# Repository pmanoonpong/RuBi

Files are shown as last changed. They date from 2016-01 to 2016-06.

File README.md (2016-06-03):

<h1>Design, simulation and development of RuBi, a bipedal platform for human-like locomotion studies</h1>

<h2>Description</h2>
RuBi is a study framework for human-like gaits part of the master thesis of Ignacio Torroba and Jorge Rodriguez. The idea is to create a robot that can perform actions like walking, running or jumping both in simulation in real life. One of the main advantages is the possibility of changing the springs in order to study SEA, PEA or SEA+PEA configurations with different springs.



In here, the description of the structure of the project is presented. The how-to for starting the simulation or bring up the robot can also be found in here. Some example controllers are given too.

It is supposed that you have a ROS Jade installed and working. This has only been tested in Ubuntu 15.04 and 14.04 under ROS Jade. To install it you can follow the official guides to be found in: http://wiki.ros.org/jade/Installation/Ubuntu. Remember that ROS Jade ONLY supports Trusty (14.04), Utopic (14.10) and Vivid (15.04) for Debian packages.

<h2>Project structure</h2>
The project has three basic folders:
  * <b>docs</b>: in here all the documents used for the deployment of the project are found. The master thesis is under the folder "report".
  * <b>media</b>: where all the media files as Photos, Videos, Presentations are stored.
  * <b>src</b>: the source folder where all the code, CAD models, robots description are.

The important folder for the user is the <b>src</b> folder and it follows the ROS structure convention. The code style is the imposed by the <i>Google Style</i> defined by the clang-code-model. The <b>build system</b> is catkin tools, and the environment is already included in the repo. This means that the user only need to clone the repo and everything will work "out-of-the-box" (notice the quotes there please).

In the source folder three kind of packages can be found:
  *   <b>ROS Jade needs</b>: Due to the use of ROS Jade, needed due to that in the description of the robots we use Jade-exclusive functions, some of the packages need to be compiled from the source. Those packages are copied as submodules in the repo and the correct branches are set with the installation script.
  *   <b>Robot descriptions</b>: Based on the Gazebo-ROS convention for describe the robots (http://gazebosim.org/tutorials/?tut=ros_overview). It is important to notice that TWO robots have been implemented: <b>RuBi</b> and <b>Dacbot</b>. Dacbot was created as a practice to finally create RuBi. Then the five folders are found for each robot.
    - robot_descrition: where all the files that describe the robot are found. If any CAD model is developed must be added in here.
    - robot_gazebo: used as a wrapper for bringing up the robot's simulation.
    - robot_bringup: used as a wrapper for bringing up the real robot.
    - robot_joint_controllers: originally called robot_controllers, though the name was change due to the lexical problem when defining "controller". This package offers the <i>joint controller</i> inside of ROS control. Ultimately what creates is a topic (e.g. /rubi/left_ankle_command) that can move the joint. This topic is then interfaced with the simulation or the real robot through a <i>hardware_interface</i>. Gazebo offers one, and the one from the real robot is called <b>locokit_hw</b> and can be found as another package within <i>src</i>.
    -   robot_controllers: Additionally, we add a new folder in which we deploy the controllers of the robot. Meaning, the controller that actually moves the robot for walking, running or jumping.
    
  *   <b>Miscellaneous</b>: these are <i>scripts</i> and <i>matlab_scripts</i>. The <b>scripts</b> folder includes the installation folder that, once the repo is cloned will download the submodules, install dependencies, etc... the <b>matlab_scripts</b> in where the actual Matlab programs used to size the motors, calculate the kinematic and dynamic models of the robot, etc.. are to be found.

<h2>First time</h2>
As explained before, inside of "src/scripts/" a script to be run the first time is found. This will download the submodules, install dependencies, etc... So:
``` bash
git clone URL_of_the_project
cd (path_to_project)/src/scripts
chmod +x install_first_time.sh
./install_first_time.sh
```
<h2>Robot definition</h2>
Inside the <i>rubi_definition</i> folder, several folders can be found. The suggested structured given in the ROS-Gazebo guides is followed. Two important things:
  * <b>CAD model</b>: the CAD model of the robot is to be found in the folder <b>meshes</b>. In here, the SolidWorks files are stored. At the same time, these follow the order of having the assembly file in the root folder and the parts in sub-folders. This will leave an assembly file called <i>Legs</i> that will load the Legs model and another one called <i>Legs with environment</i> where the robot is loaded along with the treadmill.
  * <b>Xacro</b>: the robot is defined in the URDF format. This is needed because ROS Control uses it. The robot is coded using Xacro because it simplifies the wrtting and allows conditional expression. Check the flags out inside of the <i>rubi.xacro</i> file. These add some functionality like scaling the robot or create the rotational holder, among others.

<h2>Develop controllers</h2>
In order to facilitate the development of new controllers two example controllers are given inside of RuBi. First clarify that ALL the controllers of a robot MUST be in one folder. This was decided due to the experience obtained during the use of LPZ Robots. 

To deploy a new controller just add the source into the <b>src</b> folder and add it into the CMakeList.txt. Is a ROS package, so more information can be found in Google. One of the example controllers show how to use GoRobots in it.

Remember that for using GoRobots an environmental variable called <i>GOROBOTS</i> must exist. This can be done by adding to the <i>.bashrc</i> file found in the home folder:
``` bash
export GOROBOTS=/path/to/gorobots
```

All the packages in the catkin environment are compiled introducing the next comand in any of the sub-directories of the project:
``` bash
catkin build
```

<h2>Bring up the simulation</h2>
The simulation can be loaded by opening a terminal and writing:
``` bash
roslaunch rubi_gazebo rubi.world
```
This will load the Gazebo environment, the model, the joint controllers and the plugins associated. Once finished, the controllers can be started.

<h2>Bring up the real robot</h2>
The real robot can be loaded by opening a terminal and writing:
``` bash
roslaunch rubi_bringup rubi_bringup.launch
```
This will load the Locokit interface, the model, the joint controllers and the plugins associated. Once finished, the controllers can be started.

<h2>Contributors</h2>
<b>Supervisors: </b>
  * Poramate Manoonpong: poma@mmmi.sdu.dk
  * Jørgen Christian Larsen: jcla@mmmi.sdu.dk

<b>Students: </b>
  * Jorge Rodriguez Marin: jorge.rguez.marin@gmail.com
  * Ignacio Torroba Balmori: ignaciotorroba@hotmail.com

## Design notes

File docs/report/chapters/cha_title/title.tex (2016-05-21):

%!TEX root = ../../report.tex

% Title Page
\begin{titlepage}

	\begin{center}
	\\

	\vspace{0.3cm}
	\textbf{\institute}\\

	\textmd{\department}\\
	\textmd{\program}  %- \textmd{\course}
	% \makebox[0pt][l]{
	% 	\hspace{-14cm}
	%   \raisebox{-\totalheight}[0pt][0pt]{
	%   	\includegraphics[height=180mm]{figures/legs_technical_drawing.pdf}
	%   }
	\makebox[0pt][l]{
		\hspace{-20.5cm}
	  \raisebox{-\totalheight}[0pt][0pt]{
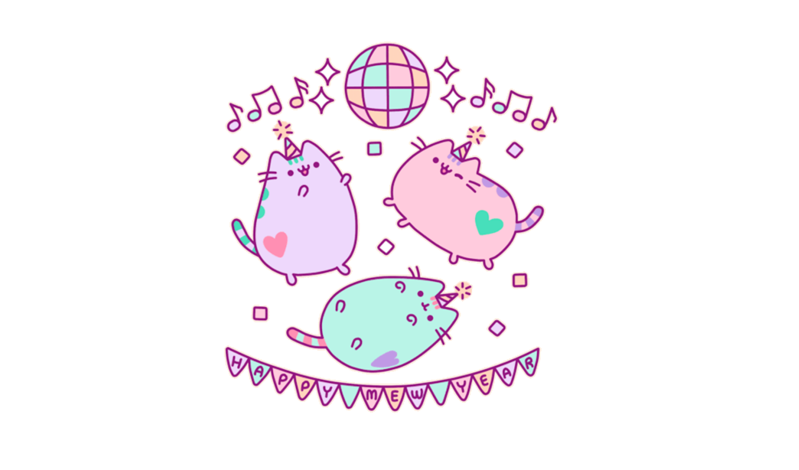
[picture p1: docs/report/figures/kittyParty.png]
	  	
	  }
	}\\[4cm]

	\vspace{0.4cm}
	{\huge \bfseries \documentTitle}
	\\
	\vspace{0.5cm}
	{\large \documentType}
	\\[2cm]

	\begin{tabular}{c}
	 \makebox[4cm]{\emph{Authors}} \\
	 \makebox[4cm]{\authorOne} \\
	 \makebox[4cm]{\authorTwo} \\
	\end{tabular}

	\vfill
	{\large \today}
	\end{center}

\end{titlepage}

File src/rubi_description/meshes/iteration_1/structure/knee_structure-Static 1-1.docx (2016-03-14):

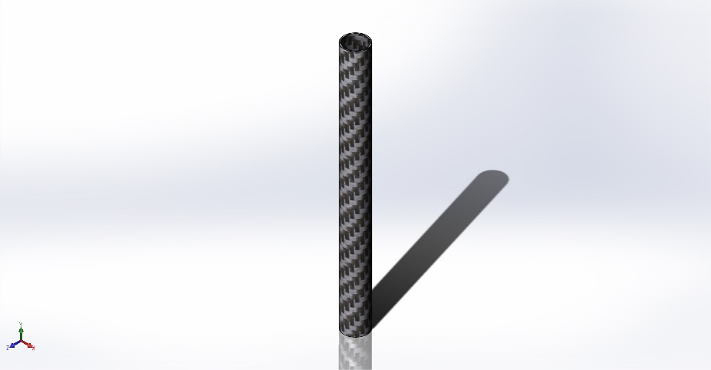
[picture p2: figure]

Simulation of knee_structure

Date: Monday, March 14, 2016
Designer: Jorge Rodriguez

Study name: Static 1

Analysis type: Static
Description No Data

# Assumptions

# Model Information

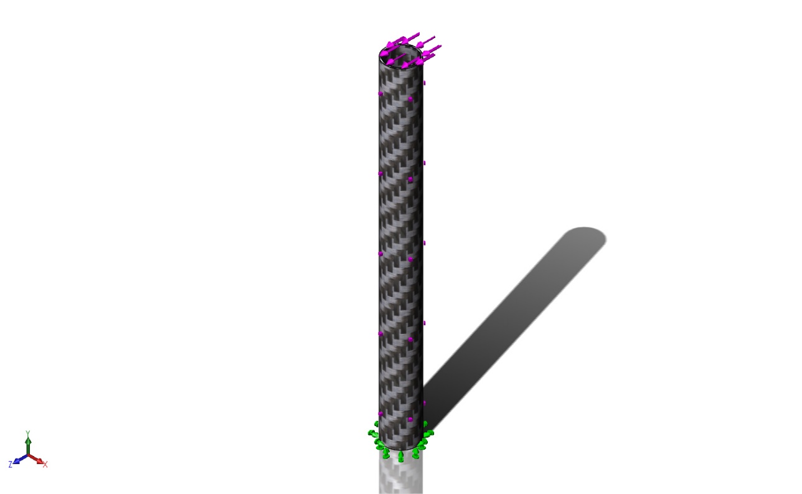
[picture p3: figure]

Model name: knee_structure

Current Configuration: Default

Solid Bodies
Document Name and Reference | Treated As | Volumetric Properties | Document Path/Date Modified

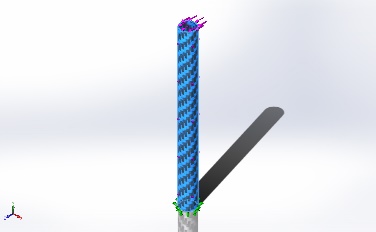
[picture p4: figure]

Boss-Extrude1 | Solid Body | Mass:0.0203042 kg Volume:1.26901e-005 m^3 Density:1600 kg/m^3 Weight:0.198982 N | D:\Drive\Projects\Legs\src\legs_description\meshes\Iteration 1\structure\knee_structure.SLDPRT Mar 13 20:21:27 2016

# Study Properties

Study name | Static 1
Analysis type | Static
Mesh type | Solid Mesh
Thermal Effect: | On
Thermal option | Include temperature loads
Zero strain temperature | 298 Kelvin
Include fluid pressure effects from SolidWorks Flow Simulation | Off
Solver type | FFEPlus
Inplane Effect: | Off
Soft Spring: | Off
Inertial Relief: | Off
Incompatible bonding options | Automatic
Large displacement | Off
Compute free body forces | Off
Friction | Off
Use Adaptive Method: | Off
Result folder | SolidWorks document (D:\Drive\Projects\Legs\src\legs_description\meshes\Iteration 1\structure)

# Units

Unit system: | SI (MKS)
Length/Displacement | mm
Temperature | Kelvin
Angular velocity | Rad/sec
Pressure/Stress | N/m^2

# Material Properties

Model Reference | Properties | Components

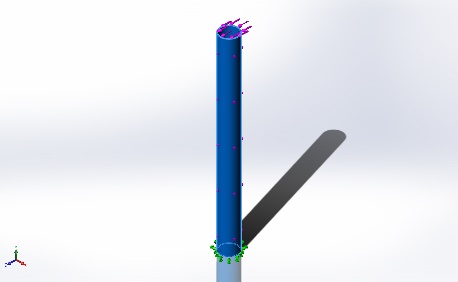
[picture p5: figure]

| Name: Toray T700 Model type: Linear Elastic Isotropic Default failure criterion: Unknown Tensile strength: 4e+008 N/m^2 Compressive strength: 3.5e+008 N/m^2 Elastic modulus: 1.9e+010 N/m^2 Poisson's ratio: 0.14 Mass density: 1600 kg/m^3 Shear modulus: 4.6e+009 N/m^2 | SolidBody 1(Boss-Extrude1)(knee_structure)

Curve Data:N/A

# Loads and Fixtures

Fixture name | Fixture Image | Fixture Details

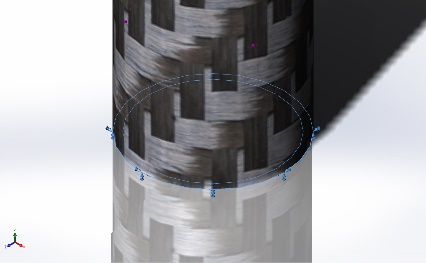
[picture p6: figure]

Fixed-1 | | Entities: 1 face(s) Type: Fixed Geometry

Resultant Forces

Components | X | Y | Z | Resultant
Reaction force(N) | 0.0268427 | 0.0375519 | -293.247 | 293.247
Reaction Moment(N.m) | 0 | 0 | 0 | 0

Load name | Load Image | Load Details

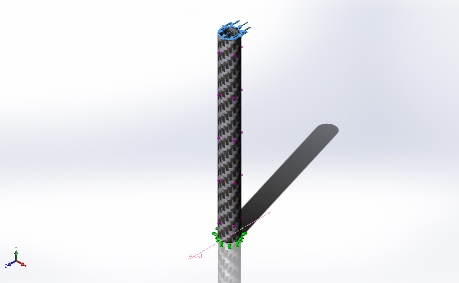
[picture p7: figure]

Force-1 | | Entities: 1 face(s) Reference: Axis1 Type: Apply force Values: ---, ---, -293.3 N

# Connector Definitions

No Data

# Contact Information

No Data

# Mesh Information

Mesh type | Solid Mesh
Mesher Used: | Curvature based mesh
Jacobian points | 4 Points
Maximum element size | 1.59686 mm
Minimum element size | 1.59686 mm
Mesh Quality | High

## Mesh Information - Details

Total Nodes | 63496
Total Elements | 31816
Maximum Aspect Ratio | 7.2328
% of elements with Aspect Ratio < 3 | 99.1
% of elements with Aspect Ratio > 10 | 0
% of distorted elements(Jacobian) | 0
Time to complete mesh(hh;mm;ss): | 00:00:04
Computer name: | JORGE-WINDOWS

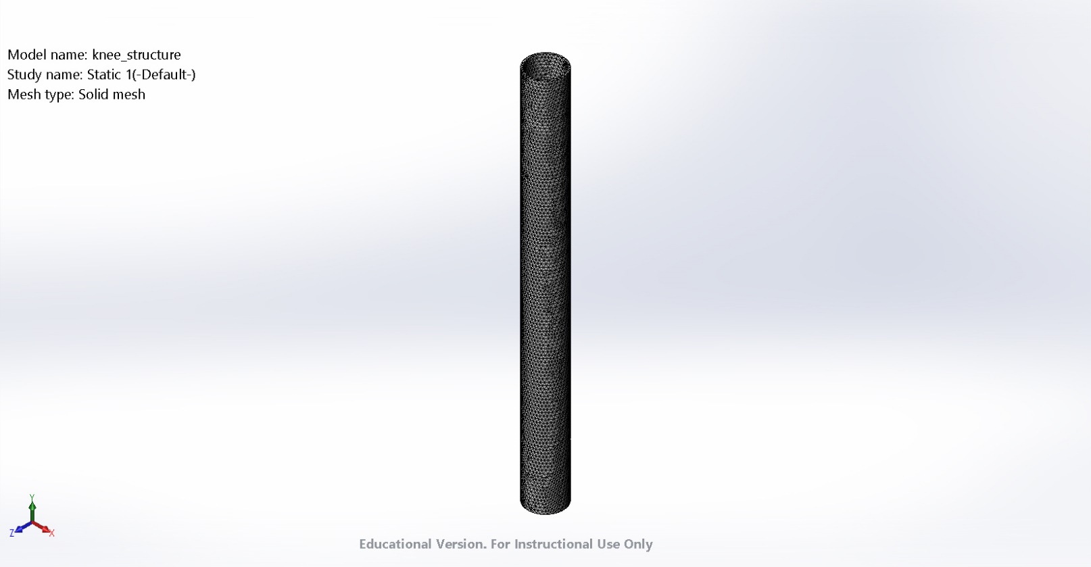
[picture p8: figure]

## Mesh Control Information:

Mesh Control Name | Mesh Control Image | Mesh Control Details

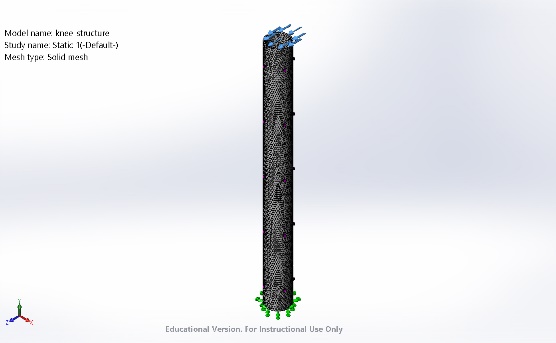
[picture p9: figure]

Control-1 | | Entities: 1 component(s) Units: mm Size: 1.59686 Ratio: 1.5

# Sensor Details

No Data

# Resultant Forces

## Reaction Forces

Selection set | Units | Sum X | Sum Y | Sum Z | Resultant
Entire Model | N | 0.0268427 | 0.0375519 | -293.247 | 293.247

## Reaction Moments

Selection set | Units | Sum X | Sum Y | Sum Z | Resultant
Entire Model | N.m | 0 | 0 | 0 | 0

# Beams

No Data

# Study Results

Name | Type | Min | Max
Stress1 | VON: von Mises Stress | 1.7183e+006 N/m^2 Node: 38677 | 2.45927e+008 N/m^2 Node: 4900

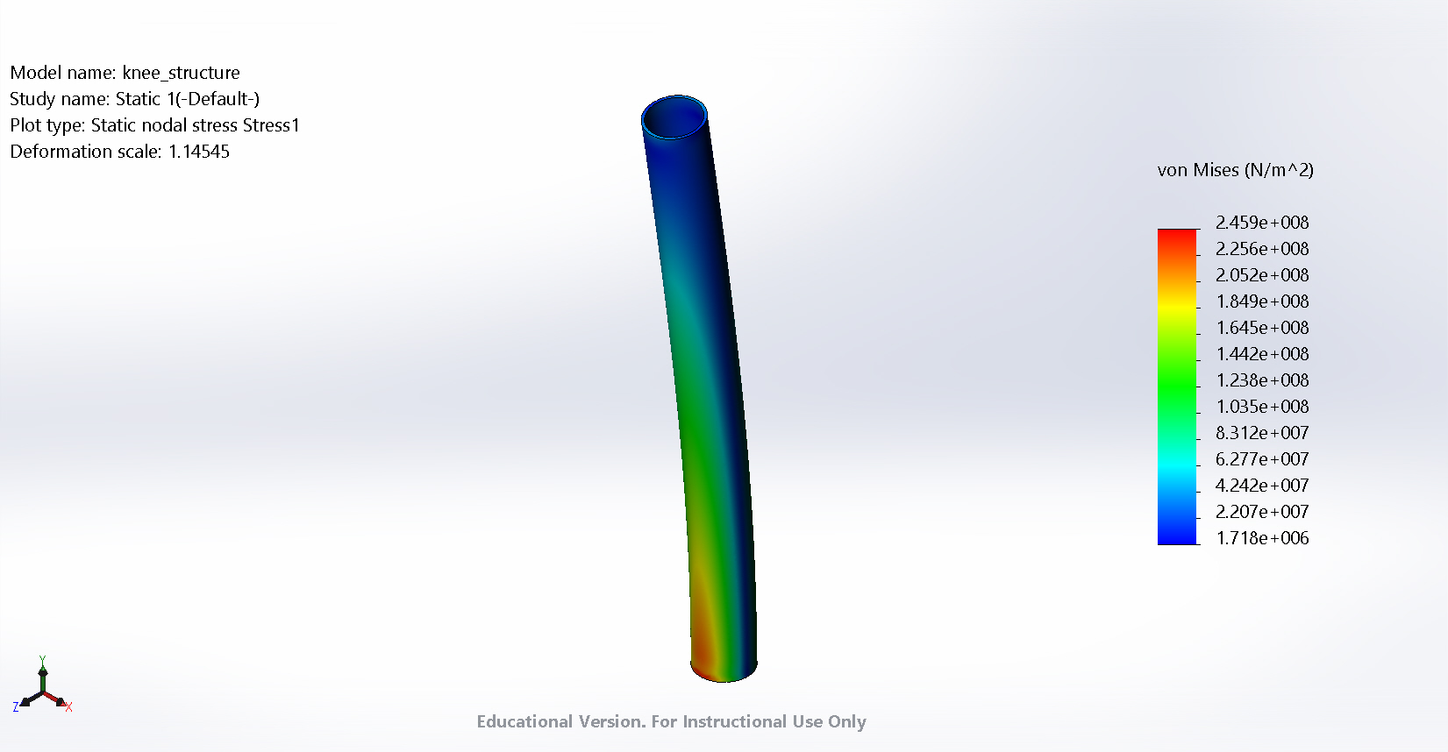
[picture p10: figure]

knee_structure-Static 1-Stress-Stress1

Name | Type | Min | Max
Displacement1 | URES: Resultant Displacement | 0 mm Node: 42 | 18.6053 mm Node: 19

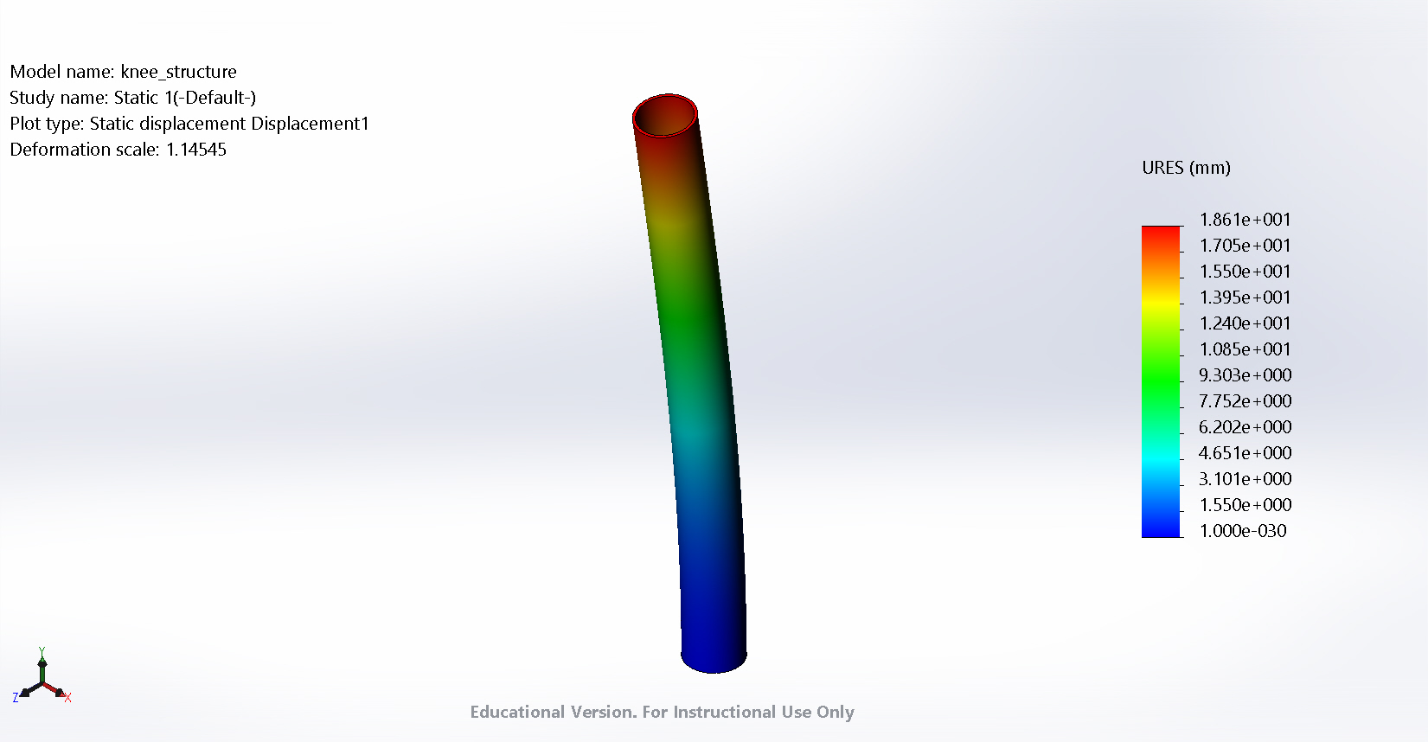
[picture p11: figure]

knee_structure-Static 1-Displacement-Displacement1

Name | Type | Min | Max
Strain1 | ESTRN: Equivalent Strain | 7.96386e-005 Element: 28451 | 0.00900996 Element: 23735

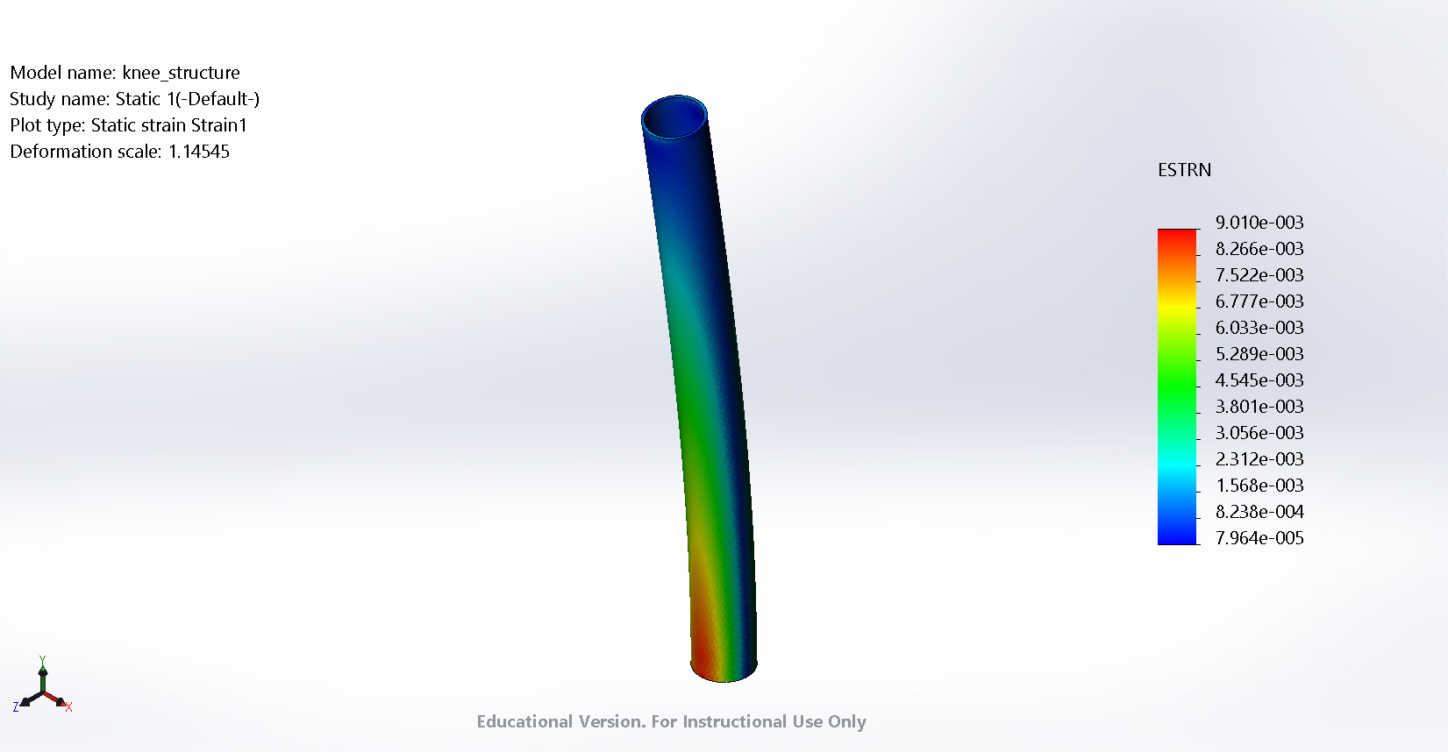
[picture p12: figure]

knee_structure-Static 1-Strain-Strain1

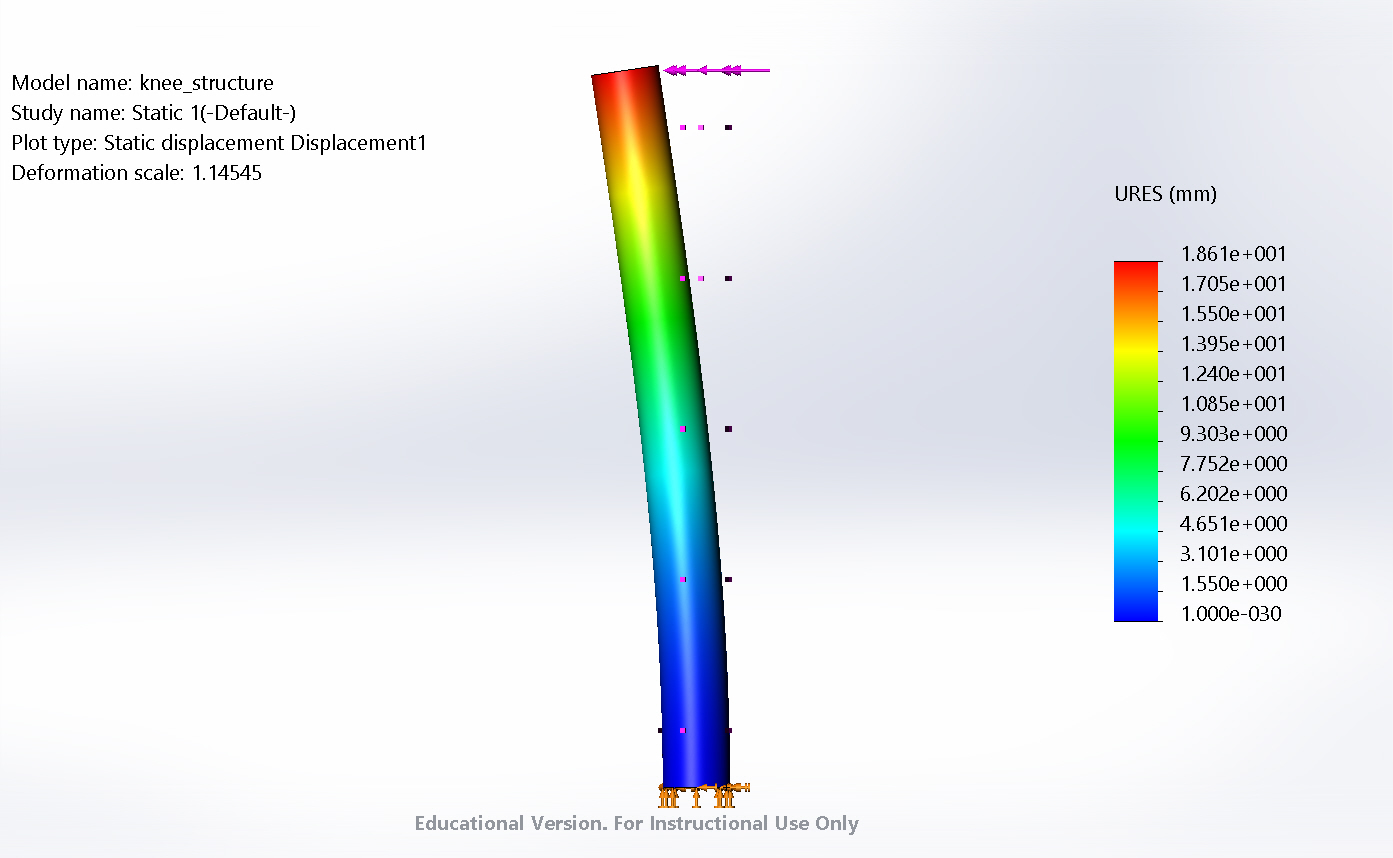
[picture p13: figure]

Image-1

# Conclusion

Analyzed with SolidWorks Simulation Simulation of knee_structure 13

Analyzed with SolidWorks Simulation Simulation of knee_structure 1

Jorge Rodriguez 14-Mar-16

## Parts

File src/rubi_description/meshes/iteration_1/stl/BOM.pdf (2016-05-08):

Part | Quantity
4 | motor_pulley_T2,5_19teeth
1 | hip
2 | hip_pinion
1 | left_hip_lower
1 | left_ankle_spring_series_with_pulley
1 | left_ankle_upper
1 | left_foot
1 | left_knee_lower
1 | left_knee_spring_series_with_pulley
1 | left_knee_upper
1 | right_hip_lower
1 | right_ankle_spring_series_with_pulley
1 | right_ankle_upper
1 | right_foot
1 | right_knee_lower
1 | right_knee_spring_series_with_pulley
1 | right_knee_upper

# BOM

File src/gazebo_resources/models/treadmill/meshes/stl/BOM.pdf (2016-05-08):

Part | Quantity
1 | Interface Robot holder
1 | Printed Parts Profile Robot
1 | Printed Parts Profile Treadmill

# BOM

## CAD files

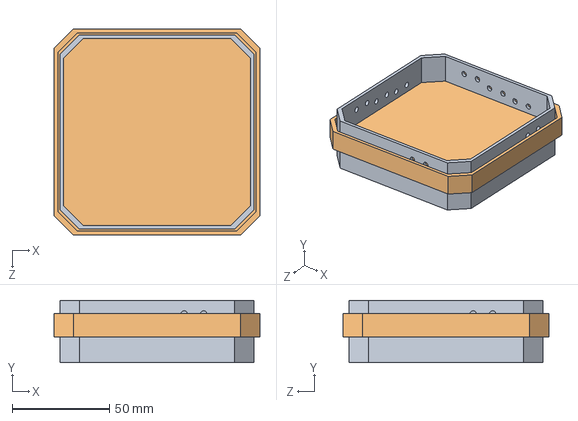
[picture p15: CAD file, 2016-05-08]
src/gazebo_resources/models/jumping_platform/meshes/Assem1.SLDASM
106.0 x 32.0 x 106.0 mm
bottom
top

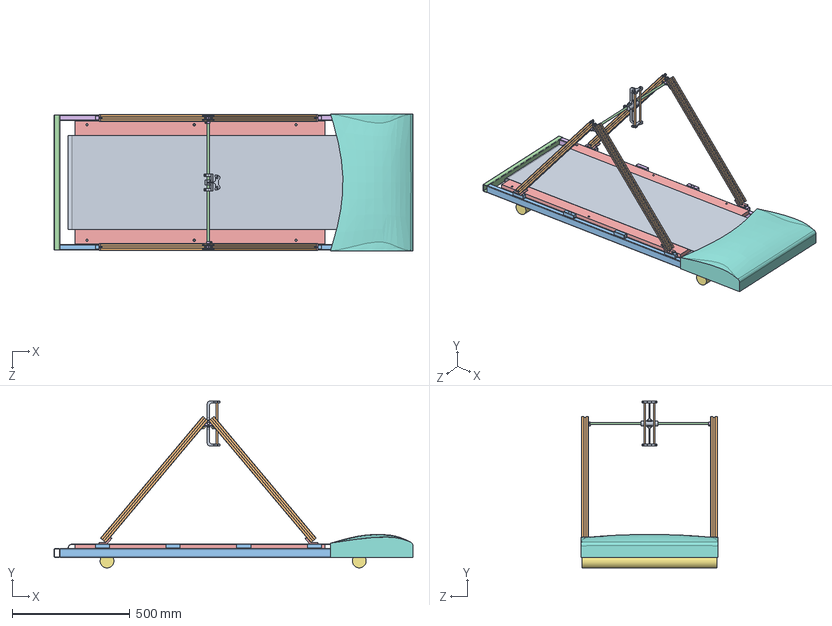
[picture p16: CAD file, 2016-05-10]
src/gazebo_resources/models/treadmill/meshes/treadmill.SLDASM
1523.0 x 707.3 x 580.0 mm
running_area
Bosch Profile - 30x30 x 4
Structure - right side
Structure - front x 2
Structure - table
MirrorStructure - right side
Structure - legs x 2
Cover
Interface - Robot holder
Interface - Jumping rods x 2
bearing_S 6000-2RS_618-9991 x 2
Interface - Structure rod
Printed Parts - Profile - Treadmill x 4
Printed Parts - Profile - Robot x 2
DIN 912 M6 x 10 --- 10N x 8
klee M3x5 x 2
DIN 912 M3 x 6 --- 6N x 2

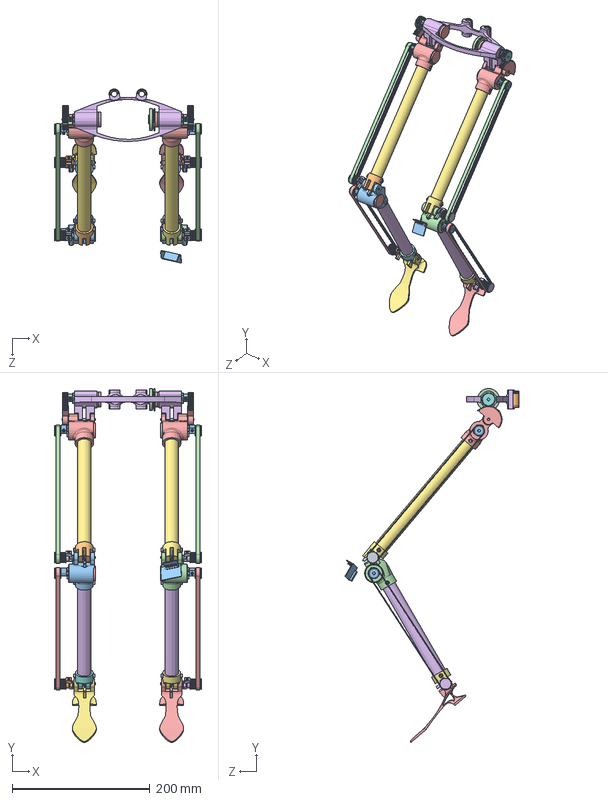
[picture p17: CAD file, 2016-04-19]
src/legs_description/meshes/iteration_1/Legs.SLDASM
213.8 x 514.5 x 253.3 mm
DIN 912 M2.5 x 8 --- 8N x 18
klee M3x5 x 18
ISO 4029 - M3 x 6-S x 18
Steel External Circlip 3mm x 8
hip_motor_holder_left x 2
hip
hip_rod x 2
hip_pinion
bearing_SS623-2RS_893-7420 x 24
Bearing - LBBR8 341-1504 x 2
T2,5 6mm 19teeth x 4
belt_gt2_hip x 2
belt_gt2_knee x 2
DIN 912 M3 x 6 --- 6N x 12
left_knee_upper
left_knee_rod x 2
left_knee_spring_series_holder
spring_knee_serial
spring_knee_parallel
knee_motor_holder_left
foot_left
foot_spring_series_holder_left
ankle_left
ankle_rod x 2
spring_ankle_parallel
spring_ankle_serial
Maxon - Gearbox 143976 x 6
Maxon - Interface x 6
knee_structure x 2
hip_structure x 2
Mirrorspring_knee_serial
Mirrorleft_knee_spring_series_holder
Mirrorleft_knee_upper
Mirrorknee_motor_holder_left
Mirrorhip_pinion
Mirrorspring_ankle_serial
Mirrorspring_ankle_parallel
Mirrorfoot_left
Mirrorankle_left
Mirrorspring_knee_parallel
Mirrorfoot_spring_series_holder_left
Maxon - Extensor

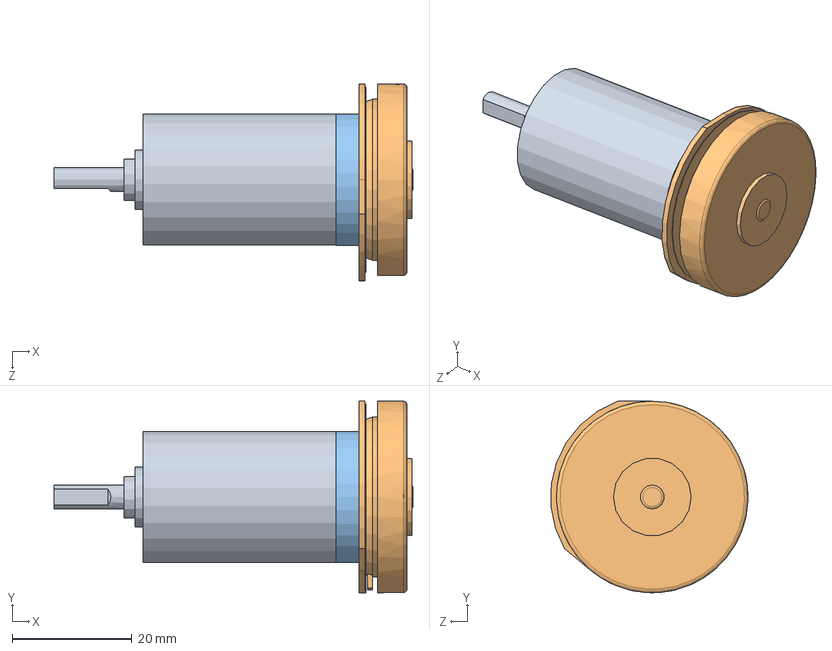
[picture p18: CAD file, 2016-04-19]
src/rubi_description/meshes/iteration_1/motors/Maxon - Combination 432941.SLDASM
60.0 x 32.0 x 32.9 mm
Maxon - Gearbox 143976
Maxon - Motor 339260
Maxon - Interface

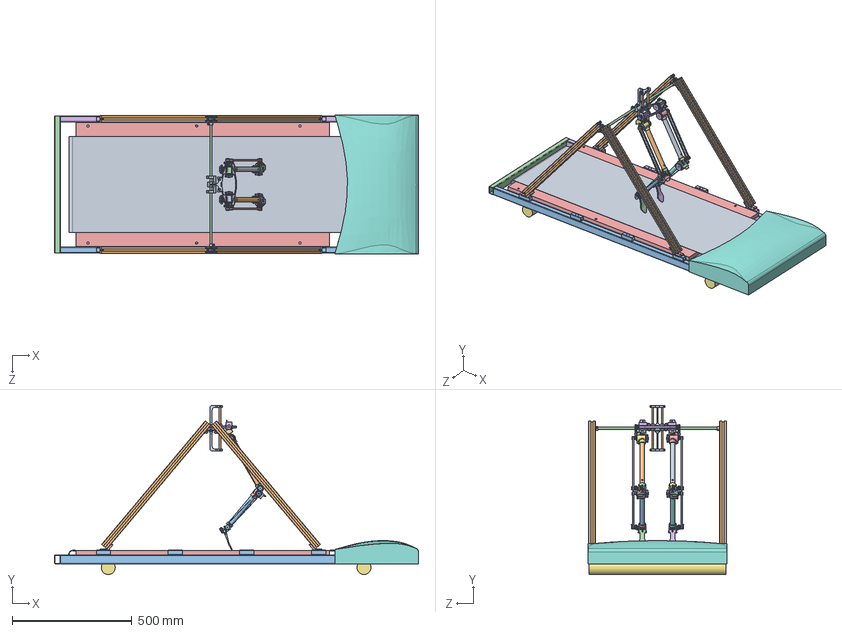
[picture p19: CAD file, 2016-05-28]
src/rubi_description/meshes/iteration_1/Rubi and Environment.SLDASM
1523.0 x 707.3 x 580.0 mm
running_area
Bosch Profile - 30x30 x 4
Structure - right side
Structure - front x 2
Structure - table
MirrorStructure - right side
Structure - legs x 2
Cover
Interface - Robot holder
Interface - Jumping rods x 2
bearing_S 6000-2RS_618-9991 x 2
Interface - Structure rod
Printed Parts - Profile - Treadmill x 4
Printed Parts - Profile - Robot x 2
DIN 912 M6 x 10 --- 10N x 8
klee M3x5 x 20
DIN 912 M3 x 6 --- 6N x 14
DIN 912 M2.5 x 8 --- 8N x 18
ISO 4029 - M3 x 6-S x 18
Steel External Circlip 3mm x 8
left_hip_lower
hip
hip_rod x 2
hip_pinion
bearing_SS623-2RS_893-7420 x 24
Bearing - LBBR8 341-1504 x 2
motor_pulley_T2,5_19teeth x 3
Maxon - Extensor x 3
belt_gt2_hip x 2
belt_gt2_knee x 2
left_knee_upper
knee_rod x 2
left_knee_spring_series_with_pulley
spring_knee_serial
spring_knee_parallel
left_knee_lower
DIN 912 M2.5 x 16 --- 16N x 4
left_foot
left_ankle_spring_series_with_pulley
left_ankle_upper
ankle_rod x 2
spring_ankle_parallel
spring_ankle_serial
Contact sensor x 2
Maxon - Gearbox 143976 x 6
Maxon - Motor 339260 x 6
Maxon - Interface x 6
knee_structure
hip_structure
Mirrorspring_knee_serial
right_knee_spring_series_with_pulley
right_knee_upper
right_knee_lower
Mirrorhip_pinion
right_hip_lower
Mirrorspring_ankle_serial
Mirrorspring_ankle_parallel
Mirrorhip_structure
Mirrorknee_structure
right_foot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

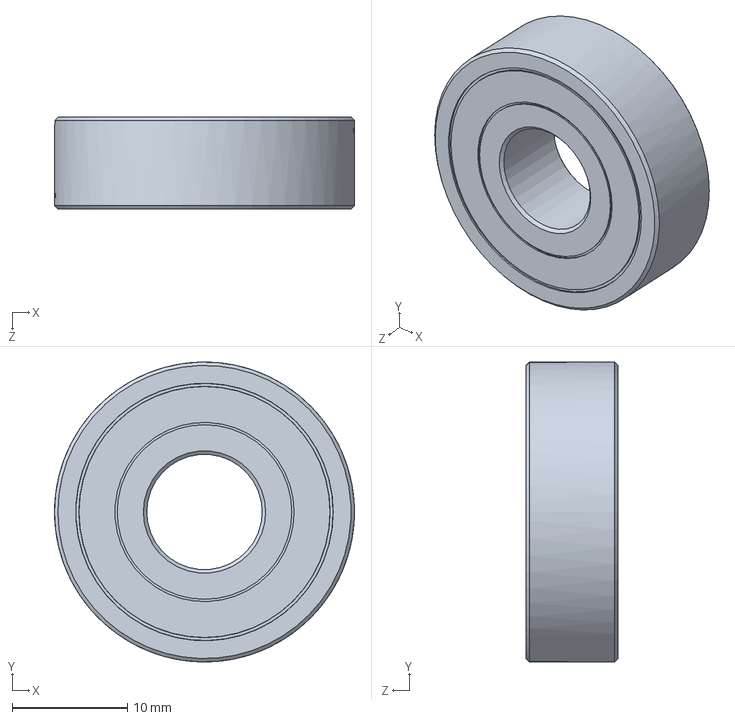
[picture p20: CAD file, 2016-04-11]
src/gazebo_resources/models/treadmill/meshes/Bearings/bearing_S 6000-2RS_618-9991.SLDPRT
26.0 x 26.0 x 8.00 mm

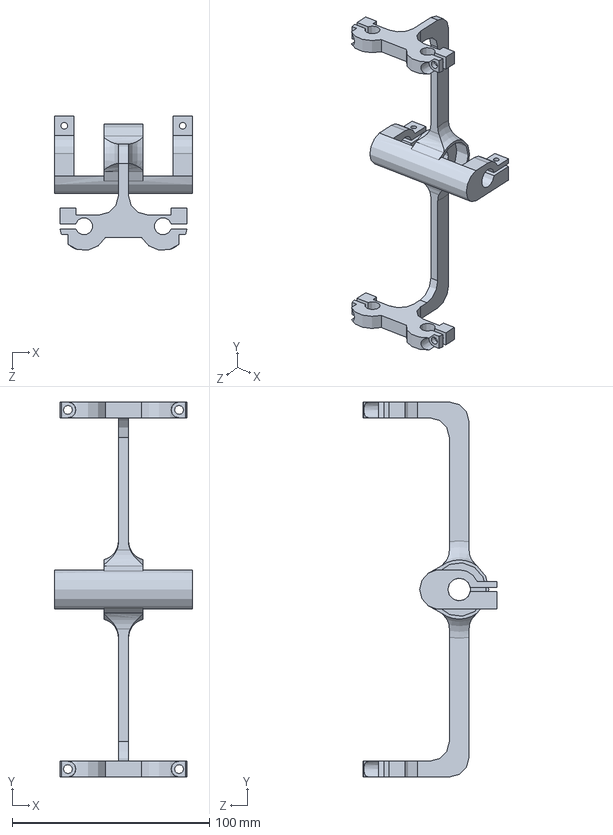
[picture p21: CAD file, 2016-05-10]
src/gazebo_resources/models/treadmill/meshes/Interface/Interface - Robot holder.SLDPRT
70.0 x 190.0 x 68.0 mm

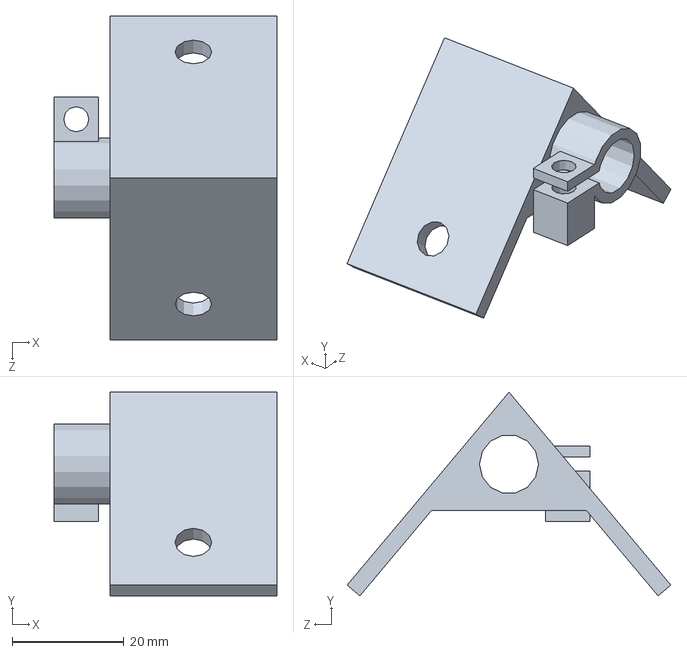
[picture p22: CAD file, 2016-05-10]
src/gazebo_resources/models/treadmill/meshes/Printed Parts/Printed Parts - Profile - Robot.SLDPRT
40.0 x 36.5 x 58.1 mm

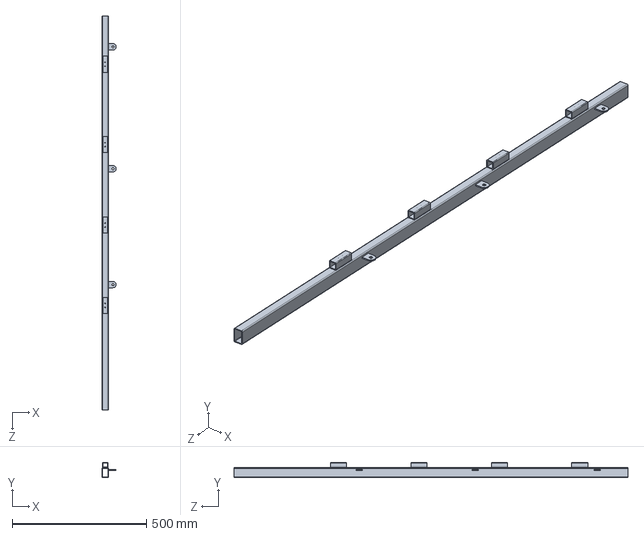
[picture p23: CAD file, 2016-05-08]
src/gazebo_resources/models/treadmill/meshes/Structure/Structure - right side.SLDPRT
54.0 x 57.0 x 1470.0 mm

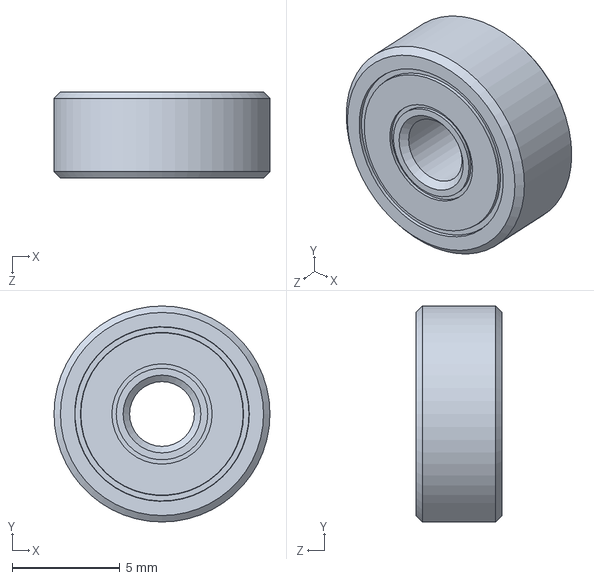
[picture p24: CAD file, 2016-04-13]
src/rubi_description/meshes/iteration_1/bearings/bearing_SS623-2RS_893-7420.SLDPRT
10.0 x 10.0 x 4.00 mm

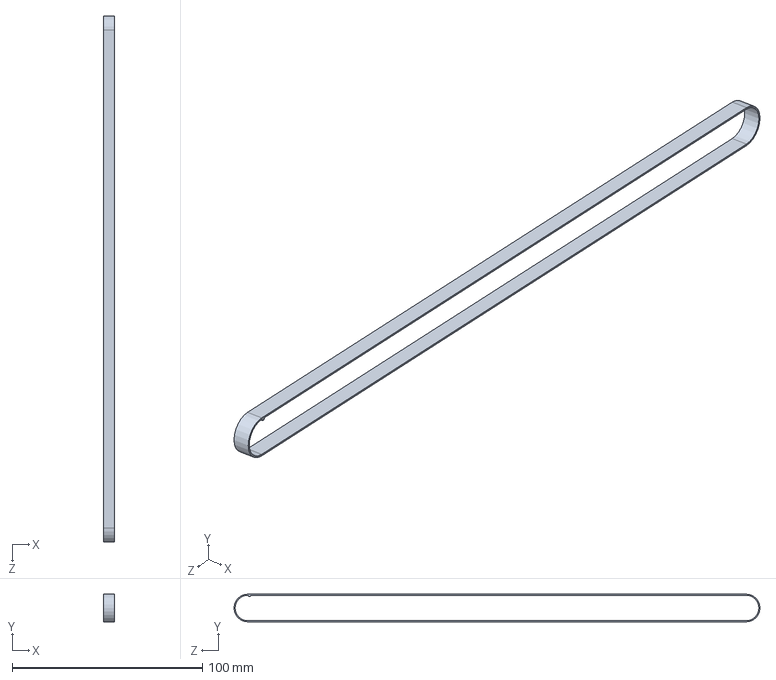
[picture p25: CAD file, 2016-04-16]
src/rubi_description/meshes/iteration_1/belt/belt_t2,5_14.6.SLDPRT
6.00 x 14.6 x 276.6 mm

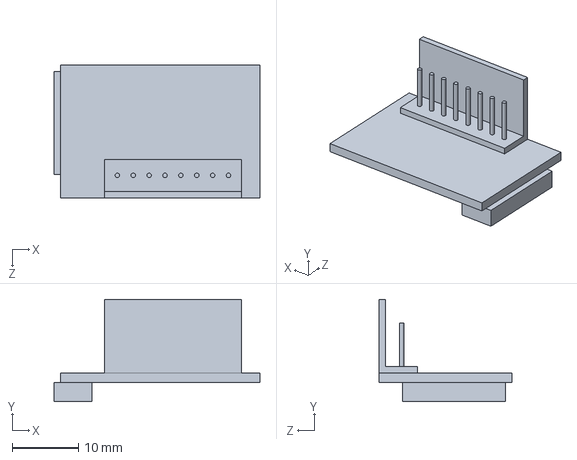
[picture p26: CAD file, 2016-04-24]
src/rubi_description/meshes/iteration_1/electronics/MirrorMaxon - Extensor.SLDPRT
31.0 x 15.4 x 20.0 mm

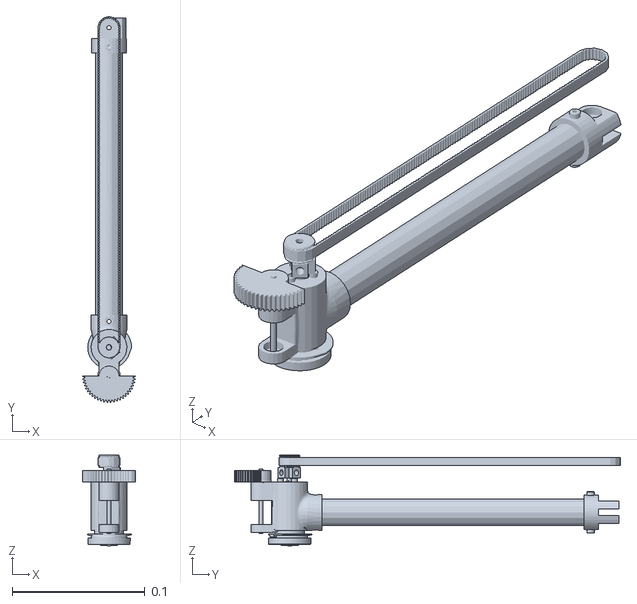
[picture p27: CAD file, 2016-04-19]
src/rubi_description/meshes/iteration_1/gazebo/left_upper_limb_visual.stl
0.04 x 0.29 x 0.0681

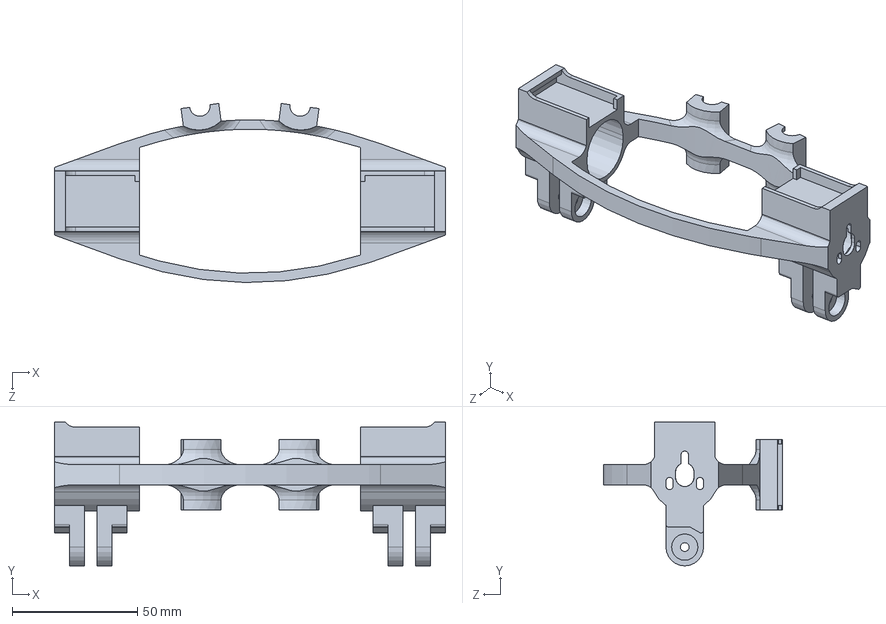
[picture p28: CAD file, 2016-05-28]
src/rubi_description/meshes/iteration_1/hip/hip.SLDPRT
156.0 x 57.4 x 71.4 mm

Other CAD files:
src/gazebo_resources/models/treadmill/meshes/stl/Printed Parts - Profile - Robot.STL
src/rubi_description/meshes/iteration_1/left_leg/ankle/left_ankle_spring_series_with_pulley.SLDPRT
src/rubi_description/meshes/iteration_1/left_leg/hip/hip_pinion.SLDPRT
src/rubi_description/meshes/iteration_1/left_leg/knee/left_knee_spring_series_with_pulley.SLDPRT
src/gazebo_resources/models/jumping_platform/meshes/bottom.SLDPRT
src/gazebo_resources/models/jumping_platform/meshes/top.SLDPRT
src/gazebo_resources/models/treadmill/meshes/Bosch Profile - 30x30.SLDPRT
src/gazebo_resources/models/treadmill/meshes/Fasteners/DIN 912 M3 x 6 --- 6N.sldprt
src/gazebo_resources/models/treadmill/meshes/Fasteners/DIN 912 M6 x 10 --- 10N.sldprt
src/gazebo_resources/models/treadmill/meshes/Interface/Interface - Jumping rods.SLDPRT
src/gazebo_resources/models/treadmill/meshes/Interface/Interface - Structure rod.SLDPRT
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

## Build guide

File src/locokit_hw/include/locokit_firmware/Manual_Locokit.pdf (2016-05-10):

## Manual Locokit over-a-network controller:

The project is made to control Locokit robot by using an interface that connects with the robot over a wireless connection. The project consists of two programs: the server program and the client program. The server program is executed on the robot's processor. The client program provides an interface that enables the user to send commands to the server to be executed. The used protocol for the connection is TCP to make sure that all transmitted information are preserved.

Running the system and establishing the connection:

The following steps demonstrate how the system should be used:

1) connecting to a wireless network:
The robot connects automatically with the wireless network “gumstix-network” and it has the IP 192.168.2.4 (the IP could be different for a different locokit robot instance). Connect the client computer to the same network and give your pc different IP address.
(for more details: http://modular.tek.sdu.dk/index.php?page=connecting-to-locokit-using-wifi)
2) Establish an SSH session:
open a terminal and write:
ssh root@192.168.2.4 (the IP could be different for a different locokit robot instance)
to open an ssh session. No password is needed for the login so just press enter when you are asked about it.
3) Run the server project:
open the following directory:
$: users/Bassel/wlan_controller
inside this folder there are the following files:
Makefile //the configuration of the compiling process actuateMotors.c //the server code
loco-settings.cfg //the robot configuration file
the code can be compiled by entering the folder and enter: make all
the compiler generate a file called “actuateMotors“
(if you are using a new instance of the robot, add those files to any directory and compile them and continue. The files can be found under utils/real_robots/locokit)
- run the server program by typing “./actuateMotors”. The server at that point will just wait for a connection from the client (socket). you should see the sentence “waiting for connections” on the terminal after running the executable file.
4) Run the Client program:

To connect the client program just open ANOTHER terminal and go to your client program executable file and run it.
NOTE: the server program should be already executed before the client program starts.
5) sending commands:
use your “LocoKitInterface” class to send and receive commands between the client and the server. The available commands will be showed in the next section.
6) Closing:
make sure that the constructor of your client LocoKitInterface object is called before you terminate your client program (i.e. use delete if you define a pointer to the object LocoKitInterface). After the client program is terminated the server program can be terminated also.

How to use the interface:

Two classes (LocoKitInterface and ConnectionClass) are provided to the user. These two classes enable the client to send commands to the server. The user should instantiate the class “LocoKitInterface” which uses the class ConnectionClass as a lower layer to send commands.

Steps:
1) define an LocoKitInterface object:

LocoKitInterface LKI; //define an object
if (LKI.establish_connection() == -1) {
printf("Error from LocoKitInterface: a connection couldn't be established...\n");
return -1;
}
2) use the available functions:
e.g. setActuatorPWM

LKI.setActuatorPWM(pmw, 2);

Available functions (Client side):

int establish_connection();
//Establish the connection with the server side. //Return 0 if successful, -1 for errors.

int setActuatorPWM(float pwm, int actuator); //Set the PWM of an actuator. //Parameters:
//pwm: The PWN in the range from -1024 to 1024 //Actuator: The ID of the actuator
//Return 0 if successful, -1 for errors.

int setActuatorStopped(int actuator); //Stop an actuator.
//Parameters:
//actuator: The ID of the actuator
//Returns: 0 if successful, -1 for errors

int setConstantSpeedInterpolatingFunction (int actuator, float period, float phaseOffset, int directionNegative);
//Set the motor control interpolation values.
//Parameters:
//actuator: The motor to control
//period: The period time in seconds
//phaseOffset: The phaseOffset in degrees
//directionNegative: The direction of rotation, 0 for rotation in positive direction 1 for negative
//Returns: 0 if successful, -1 for errors

int getNumberOfSensors();
//returns the number of sensors.
//Returns 0 if successful, -1 for errors

int getSensorValueRawFloat(int sensor, float &sensor_value);
//get the current unmodified value of the sensor (returned in the "sensor_value" parameter)
//Parameters: The ID of the sensor
//returns: 0 if successful, -1 for errors
//sensors ID numbers:
//sensor (0) ---> acc on x
//sensor (1) ---> acc on y
//sensor (2) ---> acc on z //sensor (3) ---> gyo x
//sensor (0) ---> gyo y
//sensor (0) ---> gyo z int updateSensorValueRawFloat_array();
//provides 6 values that are pointed out in the previous
//function (getSensorValueRawFloat ID:0..5) in one array and at the same order. //these values are saved in the public member sensory_inputs.
//returns 0 if successful, -1 otherwise
int | getActuatorVelocity(int | actuator, float& | velocity);
//Get the velocity of an actuator.
//Parameters:
//actuator: the ID of the actuator
//velocity: the | velocity in degrees per second in | the parameter “velocity”
//returns 0 if successful, -1 otherwise

int getActuatorPosition(int actuator, float& position);
//Get the current position of an actuator.
//Parameters:
//actuator: The ID of the actuator
//provide the position in degrees in the parameter “position” //returns 0 if successful, -1 otherwise

int getActuatorPWM(int actuator, float& PWM_value); //get the PWM of an actuator
//Parameters:
//actuator: the ID of the actuator
//provides the PWM in the parameter "PMW_value" //returns 0 if successful, -1 otherwise

int getSensorValue(int sensor, float &sensor_value); //Get current sensor value.
//Parameters:
//sensor: the ID of the sensor
//provides the current value of the sensor in the parameter "sensor_value" //returns 0 if successful, -1 otherwise

int resetSensorValue(int sensor);
////Reset a sensor. The current sensor value is used as offset for future calls to getSensorValue but not getSensorValueRaw.
//Parameters:
//sensor: the ID of the sensor
//returns 0 if successful, -1 otherwise

int terminate_connection_with_server();

//This function is called to terminate the connection with the server. It send a command to the //server to terminate the server program also

### Available Functions (Server side):

void PWM_control_routine(int act_number, float pwm);
//applying the pwm value on the targeted actuator.
It takes the actuator ID as an input in addition to the pwm value

void ConstantSpeedInterpolatingFunction_control_routine(int act_number, float period, float phaseoffset, int direction);
//applying the ConstantSpeedInterpolatingFunction values on the targeted actuator //it sets the motor control interpolation values.
//Parameters:
//actuator: The motor to control
//period: The period time in seconds
//phaseOffset: The phaseOffset in degrees
//directionNegative: the direction of rotation, 0 for rotation in positive direction 1 for negative

void setActuatorStopped_routine(int act_number);
//stop a targeted actuator. Takes the actuator number as an input

int setActuatorPWM_command(int* socket);
//receives setActuatorPWM parameters from the client and calls the required functions //to execute the command.
//It takes the connected socket numebr as an input
//return 1 if successful, -1 errors, 0 connection is closed

int setConstantSpeedInterpolatingFunction_command(int* socket); //receives setConstantSpeedInterpolatingFunction parameters from the client and calls the required functions to execute the command (ConstantSpeedInterpolatingFunction_control_routine).
//It takes the connected socket numebr as an input
//return 1 if successful, -1 errors, 0 connection is closed

int setActuatorStopped_command(int* socket);
//receives the targeted motor ID from the client and calls the required functions to execute the command (stop command for a specific motor).
//It takes the connected socket numebr as an input
//return 1 if successful, -1 errors, 0 connection is closed int getNumberOfSensors_procedure(int* socket); //calls the required functions to get the number of sensors //It takes the connected socket numebr as an input //return 1 if successful, -1 errors, 0 connection is closed

int getSensorValueRawFloat_procedure(int* socket); //receives the targeted sensor ID from the client and
//calls the required functions to execute the function //"getSensorValueRawFloat". It sends back the results to the client //It takes the connected socket numebr as an input
//return 1 if successful, -1 errors, 0 connection is closed

int getSensorValue_procedure(int* socket);
//receives the targeted sensor ID from the client and
//executes the function "getSensorValue" which get a sensor value. //It sends back the results to the client
//It takes the connected socket numebr as an input
//return 1 if successful, -1 errors, 0 connection is closed

int resetSensorValue_procedure(int* socket);
//receives the targeted sensor ID from the client and
//executes the function "resetSensorValue" which reset a sensor. //It sends back the results to the client
//It takes the connected socket numebr as an input
//return 1 if successful, -1 errors, 0 connection is closed

int getSensorValueRawFloat_array_procedure(int* socket); //executes the function "getSensorValueRawFloat" for all available sensors //to get all sensors' values.
//It sends back the results to the client as an array of 6 elements
//sensor (0) ---> acc on x
//sensor (1) ---> acc on y
//sensor (2) ---> acc on z
//sensor (3) ---> gyo x
//sensor (4) ---> gyo y
//sensor (5) ---> gyo z
//It takes the connected socket numebr as an input //return 1 if successful, -1 errors, 0 connection is closed

int getActuatorVelocity_procedure(int* socket);
//receives the targeted motor ID from the client and
//executes the function "getActuatorVelocity" which gives the motor velocity. //It sends back the results to the client

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

int getActuatorPosition_procedure(int* socket);
//receives the targeted motor ID from the client and
//executes the function "getActuatorPosition" which gives the motor position. //It sends back the results to the client
//It takes the connected socket numebr as an input
//return 1 if successful, -1 errors, 0 connection is closed

int getActuatorPWM_procedure(int* socket);
//receives the targeted motor ID from the client and
//executes the function "getActuatorPWM" which gives the motor PMW. //It sends back the results to the client
//It takes the connected socket numebr as an input
//return 1 if successful, -1 errors, 0 connection is closed

int command_interpreter(int command, int* socket); //this function represent the protocol interpreter which //interprete the commands that are coming from client.
//It takes the command number as an input and the client socket //2 ----> PWM control
//3 ----> ConstantSpeedInterpolatingFunction control
//4 ----> get Number Of Sensors
//5 ----> get Sensor Value RawFloat
//6 ----> get Sensor Value RawFloat_array (returns an array) //7 ----> get Actuator Velocity
//8 ----> get Actuator Position
//9 ----> get Actuator PWM
//10 ----> stop an Actuator //11 ----> get Sensor Value //12 ----> reset Sensor Value //50 ----> termination code

## General Notes:

1) if you are using a new instance of the robot don’t forget to modify the micro IP_Address “192.168.2.4”
to the new address in the client code.

also don’t forget to modify the loco-settings.cfg file to the new configurations of your new instance.

2) These programs use some system built-in functionalities (to open the socket, to use the connection buffers, etc). Therefore, some errors may occur. In case, you face error when connecting to the server, try please to restart your robot and your client computer and try again.
3) log file: “loco-settings.cfg” should be located on the same file in which the server executable file is located. It defines the robot's configurations which are used in the program. Any changes that you want to introduce into this file may affect the program. In addition, any hardware changes (e.g. new actuator) need to be added into this file.
4) AN example on how to use these programs is implemented for Locokit robot. The examples can be found under:
example 1: “examples/locokit/simple_control”
example 2: “examples/locokit/keyboard_control”
5) Adding more motors, use more than 4 motors
adding more index in loco-settings.cfg ARM7MC = {0, 1 | /*motor1*/, 2 /*motor2*/, 6 /*motor3*/,
12 /*motor4*/, xxx, xxx}

then you just pass the index number of the motor (the numbers that are written on the motors) that you want to send the control command to, as parameter in the function provided in the interface (e.g. setActuatorPWM).

For new robot

1) Added new network: network name (check from Locokit PC)
2) set IP address manually
3) Copy

Makefile //the configuration of the compiling process actuateMotors.c //the server code
locosettings.cfg //the robot configuration file

In locosetting.cfg
change actuator number according to a Module number used!

# Actuators (used id 0 to enable broadcast):

ARM7MC = {0, 1, 2, 6, 12}

ARM7MC = {0, module number, module number, module number, module number}

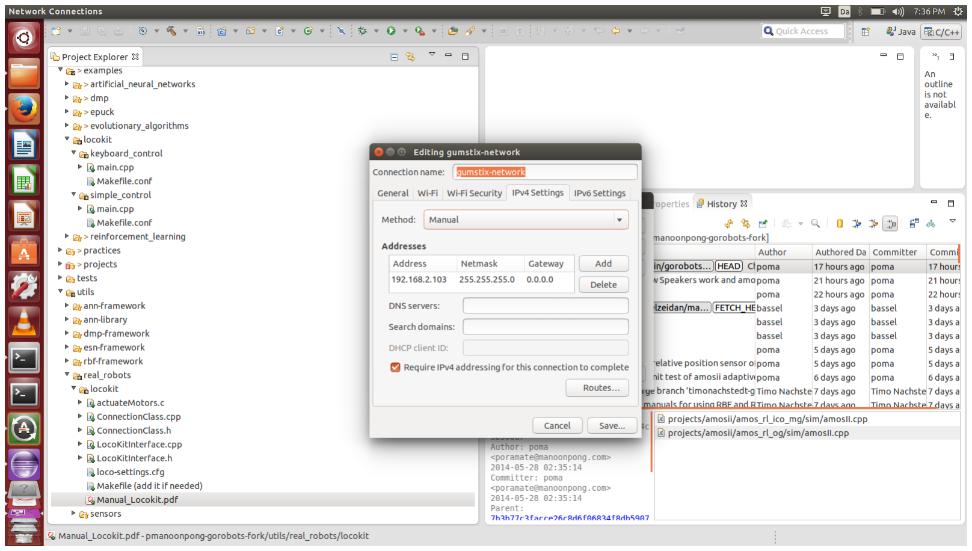
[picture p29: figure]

Locokit wireless

Getting the Gumstix onto ProjectNet and retrieving it’s ip address:
- Download ‘Putty’ for your OS version, you either use your distributions package manager (recommended) or get it from here: Putty homepage
- Attach the Locokit controller to the battery and usb port of your computer.
- Launch Putty and make a serial entry for locokit using ‘serial line’ ‘/dev/ttyUSB0’ and speed ‘115200’ [baud]
- Press ‘open’ or double click the locokit entry.
- You should now have an empty putty terminal.
- Make sure that the Locokit isn’t upside down, the Usb port should be above the power inlet.

- Activate the Locokit controller by pressing the small button on the buttom, and flicking the activation switch to a forward position.
- The putty terminal should now display the Locokit controller boot sequence.
- Once the Locokit is finished booting (it can take a good minute or two). You login with User: root and no password.
- Now it’s time to setup the network….
- Start by backing up the old wpa_supplicant.conf file by issuing the commands:
- cd /etc
- cp wpa_supplicant.conf wpa_supplicant.conf.old
- Then isssue ‘nano wpa_supplicant.conf’ and remove all but the first network entry.
- change the ssid from “locomorph” to “ProjectNet”, and psk to “robot.er.godt”
- Then press control+X and save the modified wpa_supplicant.conf
- You can now use ifdown and ifup to hook up to the ProjectNet wlan, and ifconfig to retrieve the network address. (see: Gumstix Overo_Wifi setup for more info)
Now you are ready to play around with the Lpzrobot interface! See the provided manual for more info.

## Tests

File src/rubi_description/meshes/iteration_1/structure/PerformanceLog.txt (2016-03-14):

Processing material properties:  0 hr 0 min 0 sec
Processing element groups:  0 hr 0 min 0 sec
Processing drop test gap nodes:  0 hr 0 min 0 sec
Updating thickness for shell regions:  0 hr 0 min 0 sec
Processing rconst for elements:  0 hr 0 min 0 sec
Processing egroups:  0 hr 0 min 0 sec
Transferring loads and boundary conditions:  0 hr 0 min 0 sec
Generating contacts:  0 hr 0 min 0 sec
Transfer SL1 data:  0 hr 0 min 0 sec
Generate more accurate contact data:  0 hr 0 min 0 sec
Number of contact data: 0
Transfer beam/joint contact data:  0 hr 0 min 0 sec
Transferring other special loads:  0 hr 0 min 0 sec
Transferring bearing loads:  0 hr 0 min 0 sec
Transferring mass elements:  0 hr 0 min 0 sec
Transferring point loads:  0 hr 0 min 0 sec
Transferring distributed beam loads:  0 hr 0 min 0 sec
Transferring rigid bodies:  0 hr 0 min 0 sec
Transferring component no penetration:  0 hr 0 min 0 sec
Writing Data:  0 hr 0 min 0 sec
Transferring analysis options:  0 hr 0 min 0 sec
Total midsurf mapping:  0 hr 0 min 0 sec

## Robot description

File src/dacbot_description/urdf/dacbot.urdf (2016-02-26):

<?xml version="1.0" ?>
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
<robot name="dacbot" xmlns:xacro="http://www.ros.org/wiki/xacro">
  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
  <link name="left_foot">
    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
    <inertial>
      <origin rpy="0 -1.57079632679 0" xyz="0.004 0.01 0"/>
      <mass value="0.01"/>
      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
    </inertial>
  </link>
  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
  <link name="left_lower_leg">
    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
    <inertial>
      <origin rpy="0 -1.57079632679 0" xyz="0.0625 0 0"/>
      <mass value="0.08"/>
      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
    </inertial>
  </link>
  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
  <link name="left_upper_leg">
    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
    <inertial>
      <origin rpy="0 -1.57079632679 0" xyz="0.071 0 0"/>
      <mass value="0.2"/>
      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
    </inertial>
  </link>
  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
  <link name="right_foot">
    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
    <inertial>
      <origin rpy="0 -1.57079632679 0" xyz="0.004 0.01 0"/>
      <mass value="0.01"/>
      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
    </inertial>
  </link>
  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
  <link name="right_lower_leg">
    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
    <inertial>
      <origin rpy="0 -1.57079632679 0" xyz="0.0625 0 0"/>
      <mass value="0.08"/>
      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
    </inertial>
  </link>
  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
  <link name="right_upper_leg">
    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
    <inertial>
      <origin rpy="0 -1.57079632679 0" xyz="0.071 0 0"/>
      <mass value="0.2"/>
      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
    </inertial>
  </link>
  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
  <link name="body">
    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
    <inertial>
      <origin rpy="0 0 0" xyz="0 0 0.0325"/>
      <mass value="0.45"/>
      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
    </inertial>
  </link>
  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
  <link name="world"/>
  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
  <joint name="left_hip" type="revolute">
    <parent link="body"/>
    <child link="left_upper_leg"/>
    <origin rpy="0 1.57079632679 0" xyz="-0.015 0 0"/>
    <axis xyz="0 0 1"/>
    <limit effort="10" lower="-0.523598775598" upper="0.523598775598" velocity="10"/>
    <dynamics damping="0.7"/>
  </joint>
  <joint name="left_knee" type="revolute">
    <parent link="left_upper_leg"/>
    <child link="left_lower_leg"/>
    <origin rpy="0 0 0" xyz="0.142 0 0"/>
    <axis xyz="0 0 1"/>
    <limit effort="10" lower="-2.61799387799" upper="0.0" velocity="10"/>
    <dynamics damping="0.7"/>
  </joint>
  <joint name="left_ankle" type="revolute">
    <parent link="left_lower_leg"/>
    <child link="left_foot"/>
    <origin rpy="0 0 0" xyz="0.125 0 0"/>
    <axis xyz="0 0 1"/>
    <limit effort="10" lower="0" upper="0" velocity="10"/>
    <dynamics damping="0.7"/>
  </joint>
  <joint name="right_hip" type="revolute">
    <parent link="body"/>
    <child link="right_upper_leg"/>
    <origin rpy="0 1.57079632679 0" xyz="0.015 0 0"/>
    <axis xyz="0 0 1"/>
    <limit effort="10" lower="-0.523598775598" upper="0.523598775598" velocity="10"/>
    <dynamics damping="0.7"/>
  </joint>
  <joint name="right_knee" type="revolute">
    <parent link="right_upper_leg"/>
    <child link="right_lower_leg"/>
    <origin rpy="0 0 0" xyz="0.142 0 0"/>
    <axis xyz="0 0 1"/>
    <limit effort="10" lower="-2.61799387799" upper="0.0" velocity="10"/>
    <dynamics damping="0.7"/>
  </joint>
  <joint name="right_ankle" type="revolute">
    <parent link="right_lower_leg"/>
    <child link="right_foot"/>
    <origin rpy="0 0 0" xyz="0.125 0 0"/>
    <axis xyz="0 0 1"/>
    <limit effort="10" lower="0" upper="0" velocity="10"/>
    <dynamics damping="0.7"/>
  </joint>
  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
  <link name="rotational_robot_holder_base">
    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
    <inertial>
      <mass value="10"/>
      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
    </inertial>
  </link>
  <link name="rotational_robot_holder_virtual">
    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
    <inertial>
      <mass value="0.01"/>
      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
    </inertial>
  </link>
  <link name="rotational_robot_holder_holder">
    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
    <inertial>
      <mass value="0.01"/>
      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
    </inertial>
  </link>
  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
  <joint name="rotational_robot_holder_base_to_world" type="fixed">
    <parent link="world"/>
    <child link="rotational_robot_holder_base"/>
    <origin rpy="0 0 0" xyz="0 0 0.1875"/>
  </joint>
  <joint name="rotational_robot_holder_virtual_to_holder" type="fixed">
    <parent link="rotational_robot_holder_base"/>
    <child link="rotational_robot_holder_virtual"/>
  </joint>
  <joint name="rotational_robot_holder_joint" type="fixed">
    <parent link="rotational_robot_holder_virtual"/>
    <child link="rotational_robot_holder_holder"/>
    <origin rpy="0 0 0" xyz="0 0 0.1875"/>
  </joint>
  <joint name="rotational_robot_holder_to_rotot" type="fixed">
    <parent link="rotational_robot_holder_holder"/>
    <child link="body"/>
    <origin rpy="0 0 0" xyz="2.0425 0 0"/>
    <axis xyz="0 0 1"/>
    <limit effort="30" lower="0" upper="1" velocity="1.0"/>
  </joint>
</robot>

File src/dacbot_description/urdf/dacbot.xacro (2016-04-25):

<?xml version="1.0"?>

<robot name="dacbot" xmlns:xacro="http://www.ros.org/wiki/xacro">

	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
	<xacro:property name="PI" value="3.1415926535897931"/>
	<xacro:property name="DEG_TO_RAD" value="${PI/180}"/>

	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
	<xacro:property name="update_rate" value="10"/>
	<xacro:property name="robot_name" value="dacbot"/>

  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
  <xacro:property name="robot_floating" value="0"/>

	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
	<xacro:property name="max_real_motor_torque" value="1.0787315"/> 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
  <xacro:property name="scale" value="1" />
  <xacro:property name="minimum_intertia" value="2e-03" /> 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

	<xacro:property name="bodyWidth" value="${0.085*scale}" />
	<xacro:property name="bodyLength" value="${0.08*scale}" />
	<xacro:property name="bodyHeight" value="${0.065*scale}" />
	<xacro:property name="bodyMass" value="${0.45*scale}" />

	<xacro:property name="weightWidth" value="${0.05*scale}" />
	<xacro:property name="weightLength" value="${0.07*scale}" />
	<xacro:property name="weightHeight" value="${0.025*scale}" />
	<xacro:property name="weightMass" value="${0.50*scale}" />

	<xacro:property name="upperLegWidth" value="${0.015*scale}" />
	<xacro:property name="upperLegLength" value="${0.015*scale}" />
	<xacro:property name="upperLegHeight" value="${0.142*scale}" />
	<xacro:property name="upperLegMass" value="${0.2*scale}" />
  <xacro:property name="upperLegLimitUpperPosition" value="30" />
  <xacro:property name="upperLegLimitLowerPosition" value="-30" />
  <xacro:property name="upperLegLimitVelocity" value="10" />
  <xacro:property name="upperLegLimitEffort" value="10" />
  <xacro:property name="upperLegDamping" value="0.7" />

	<xacro:property name="lowerLegWidth" value="${0.015*scale}" />
	<xacro:property name="lowerLegLength" value="${0.015*scale}" />
	<xacro:property name="lowerLegHeight" value="${0.125*scale}" />
	<xacro:property name="lowerLegMass" value="${0.08*scale}" />
  <xacro:property name="lowerLegLimitUpperPosition" value="0" />
  <xacro:property name="lowerLegLimitLowerPosition" value="-150" />
  <xacro:property name="lowerLegLimitVelocity" value="10" />
  <xacro:property name="lowerLegLimitEffort" value="10" />
  <xacro:property name="lowerLegDamping" value="0.7" />

	<xacro:property name="footWidth" value="${0.015*scale}" />
	<xacro:property name="footLength" value="${0.050*scale}" />
	<xacro:property name="footHeight" value="${0.008*scale}" />
	<xacro:property name="footMass" value="${0.01*scale}" />
  <xacro:property name="footLimitUpperPosition" value="0" />
  <xacro:property name="footLimitLowerPosition" value="0" />
  <xacro:property name="footLimitVelocity" value="10" />
  <xacro:property name="footLimitEffort" value="10" />
  <xacro:property name="footDamping" value="0.7" />

	<xacro:property name="legDistFromCenter" value="${0.015*scale}" />

	<xacro:property name="footAnklePos" value="${0.015*scale}" />
	<xacro:property name="legAnklePos" value="${0*scale}" />
	<xacro:property name="lowerKneePos" value="${0.12*scale}" />
	<xacro:property name="upperKneePos" value="${0.02*scale}" />
	<xacro:property name="legHipPos" value="${0.132*scale}" />
	<xacro:property name="bodyHipHeight" value="${0.01*scale}" />
	<xacro:property name="bodyHipWidth" value="${0.025*scale}" />

	<xacro:property name="massJointBodyDepth" value="${0.07*scale}" />
	<xacro:property name="massJointBodyHeight" value="${0.055*scale}" />
	<xacro:property name="massJointMassDepth" value="${0.065*scale}" />
	<xacro:property name="massJointMassHeigth" value="${0.007*scale}" />

	<xacro:property name="armLength" value="${0.6*scale}" />
	<xacro:property name="armOffset" value="${0.025*scale}" />


	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
	<xacro:include filename="$(find dacbot_description)/urdf/dacbot.gazebo" />
	<xacro:include filename="$(find dacbot_description)/urdf/colors.xacro" />


	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
	<xacro:macro name="create_box" params="name origin_x origin_y origin_z r p y width length height mass">

		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
		<xacro:property name="ixx" value="${minimum_intertia}" />
		<xacro:if value="${mass / 12.0 * (length*length + height*height) > 0.01}">
			<xacro:property name="ixx" value="${mass / 12.0 * (length*length + height*height)}" />
		</xacro:if>

		<xacro:property name="iyy" value="${minimum_intertia}" />
		<xacro:if value="${mass / 12.0 * (length*length + height*height) > 0.01}">
			<xacro:property name="iyy" value="${mass / 12.0 * (length*length + height*height)}" />
		</xacro:if>

		<xacro:property name="izz" value="${minimum_intertia}" />
		<xacro:if value="${mass / 12.0 * (length*length + height*height) > 0.01}">
			<xacro:property name="izz" value="${mass / 12.0 * (length*length + height*height)}" />
		</xacro:if>

		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
		<link name="${name}">
			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

			<inertial>
				<origin xyz="${origin_x} ${origin_y} ${origin_z}" rpy="${r} ${p} ${y}"/>
				<mass value="${mass}"/>
				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
			</inertial>
		</link>
	</xacro:macro>



	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
	<xacro:create_box name="left_foot" origin_x="${footHeight/2}" origin_y="${footLength/2 - footAnklePos}" origin_z="0" r="0" p="${-PI/2}" y="0" width="${footWidth}" length="${footLength}" height="${footHeight}" mass="${footMass}" />

	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
	<xacro:create_box name="left_lower_leg" origin_x="${lowerLegHeight/2}" origin_y="0" origin_z="0" r="0" p="${-PI/2}" y="0" width="${lowerLegWidth}" length="${lowerLegLength}" height="${lowerLegHeight}" mass="${lowerLegMass}" />

	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
	<xacro:create_box name="left_upper_leg" origin_x="${upperLegHeight/2}" origin_y="0" origin_z="0" r="0" p="${-PI/2}" y="0" width="${upperLegWidth}" length="${upperLegLength}" height="${upperLegHeight}" mass="${upperLegMass}" />


	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
	<xacro:create_box name="right_foot" origin_x="${footHeight/2}" origin_y="${footLength/2 - footAnklePos}" origin_z="0" r="0" p="${-PI/2}" y="0" width="${footWidth}" length="${footLength}" height="${footHeight}" mass="${footMass}" />

	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
	<xacro:create_box name="right_lower_leg" origin_x="${lowerLegHeight/2}" origin_y="0" origin_z="0" r="0" p="${-PI/2}" y="0" width="${lowerLegWidth}" length="${lowerLegLength}" height="${lowerLegHeight}" mass="${lowerLegMass}" />

	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
	<xacro:create_box name="right_upper_leg" origin_x="${upperLegHeight/2}" origin_y="0" origin_z="0" r="0" p="${-PI/2}" y="0" width="${upperLegWidth}" length="${upperLegLength}" height="${upperLegHeight}" mass="${upperLegMass}" />


	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
	<xacro:create_box name="body" origin_x="0" origin_y="0" origin_z="${bodyHeight/2}" r="0" p="0" y="0" width="${bodyWidth}" length="${bodyLength}" height="${bodyHeight}" mass="${bodyMass}" />

	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
  <link name="world"/>

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


	<joint name="left_hip" type="revolute">
		<parent link="body"/>
		<child link="left_upper_leg"/>
		<origin xyz="${-legDistFromCenter} 0 0" rpy="0 ${PI/2} 0"/>
		<axis xyz="0 0 1"/>
		<limit effort="${upperLegLimitEffort}" velocity="${upperLegLimitVelocity}" lower="${upperLegLimitLowerPosition*DEG_TO_RAD}" upper="${upperLegLimitUpperPosition*DEG_TO_RAD}" />
		<dynamics damping="${upperLegDamping}"/>
	</joint> 

	<joint name="left_knee" type="revolute">
		<parent link="left_upper_leg"/>
		<child link="left_lower_leg"/>
		<origin xyz="${upperLegHeight} 0 0" rpy="0 0 0"/>
		<axis xyz="0 0 1"/>
		<limit effort="${lowerLegLimitEffort}" velocity="${lowerLegLimitVelocity}" lower="${lowerLegLimitLowerPosition*DEG_TO_RAD}" upper="${lowerLegLimitUpperPosition*DEG_TO_RAD}" />
		<dynamics damping="${lowerLegDamping}"/>
	</joint>

	<joint name="left_ankle" type="revolute">
		<parent link="left_lower_leg"/>
		<child link="left_foot"/>
		<origin xyz="${lowerLegHeight} 0 0" rpy="0 0 0"/>
		<axis xyz="0 0 1"/>
		<limit effort="${footLimitEffort}" velocity="${footLimitVelocity}" lower="${footLimitLowerPosition}" upper="${footLimitUpperPosition}" />
		<dynamics damping="${footDamping}"/>
	</joint>
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

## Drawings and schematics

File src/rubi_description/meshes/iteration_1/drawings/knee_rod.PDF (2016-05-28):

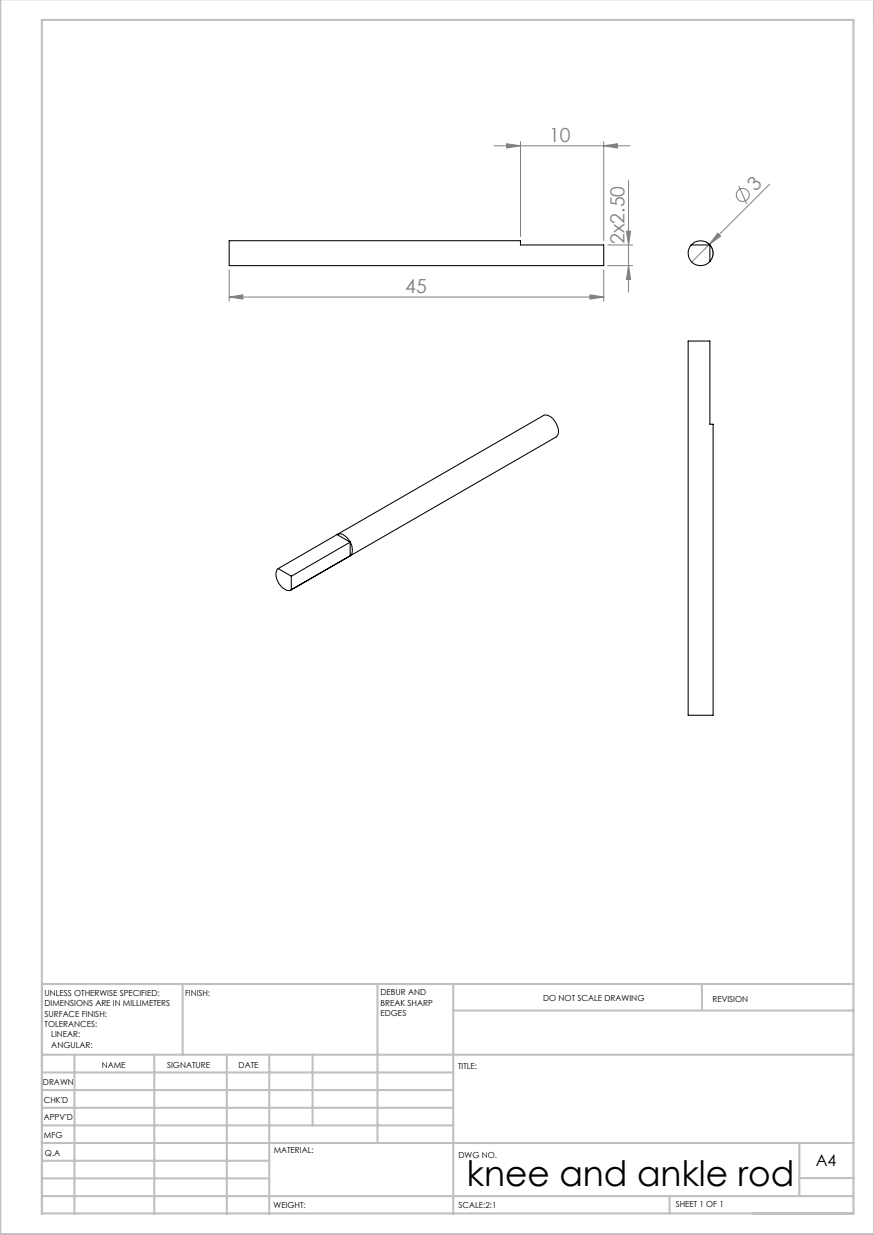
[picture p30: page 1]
SCALE:2:1; SHEET 1 OF 1; DO NOT SCALE DRAWING; REVISION; DEBUR AND BREAK SHARP; UNLESS OTHERWISE SPECIFIED:; FINISH:

DIMENSIONS ARE IN MILLIMETERS
SURFACE FINISH:
TOLERANCES:
LINEAR:
ANGULAR:

NAME | SIGNATURE | DATE | | | | TITLE:
Q.A | | | | MATERIAL: | DWG NO. knee and ankle rod WEIGHT: | A4

DRAWN
CHK'D
APPV'D
MFG

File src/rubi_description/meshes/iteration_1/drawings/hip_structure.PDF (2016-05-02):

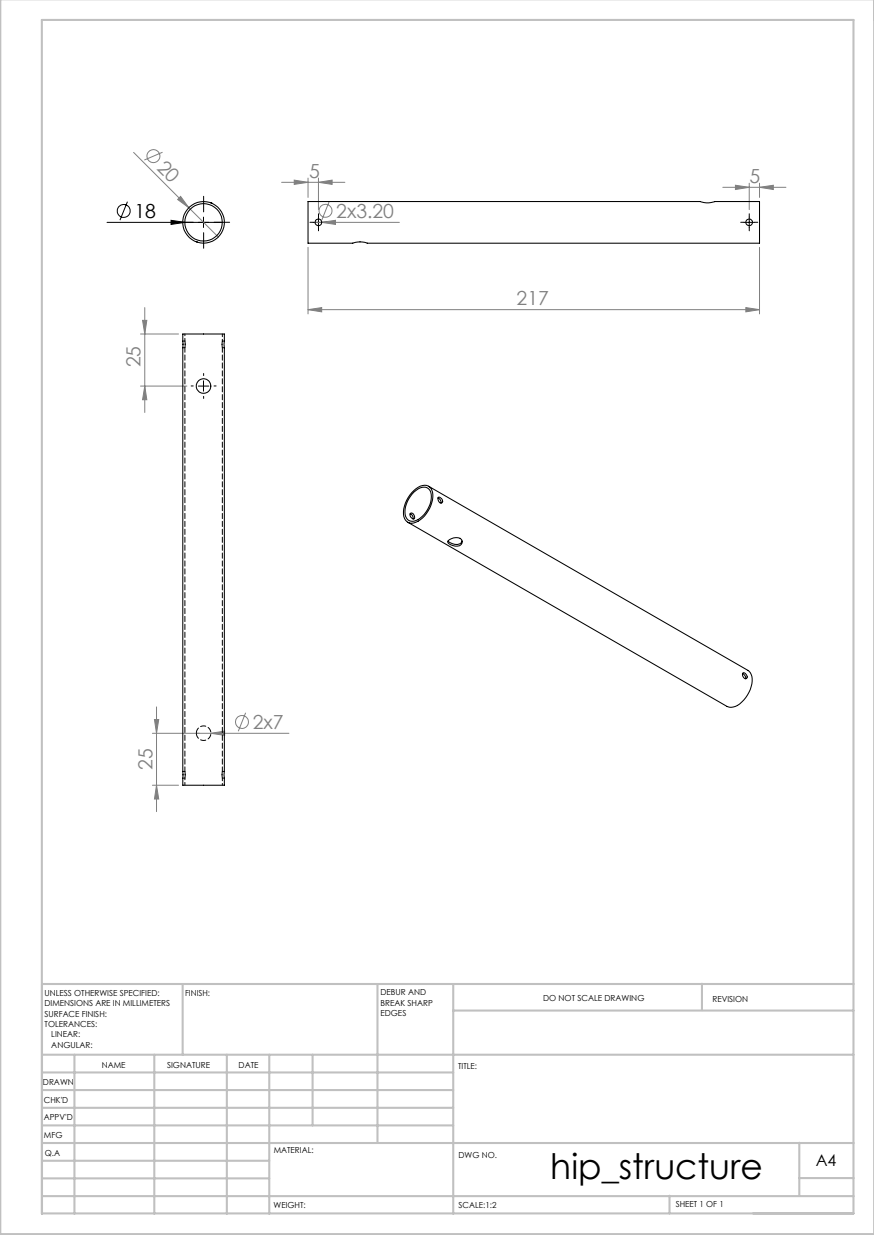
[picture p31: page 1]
SCALE:1:2; SHEET 1 OF 1; DO NOT SCALE DRAWING; REVISION; DEBUR AND BREAK SHARP; UNLESS OTHERWISE SPECIFIED:; FINISH:

DIMENSIONS ARE IN MILLIMETERS
SURFACE FINISH:
TOLERANCES:
LINEAR:
ANGULAR:

NAME | SIGNATURE | DATE | | | | TITLE:
Q.A | | | | MATERIAL: | hip_structure WEIGHT: DWG NO. | A4

DRAWN
CHK'D
APPV'D
MFG

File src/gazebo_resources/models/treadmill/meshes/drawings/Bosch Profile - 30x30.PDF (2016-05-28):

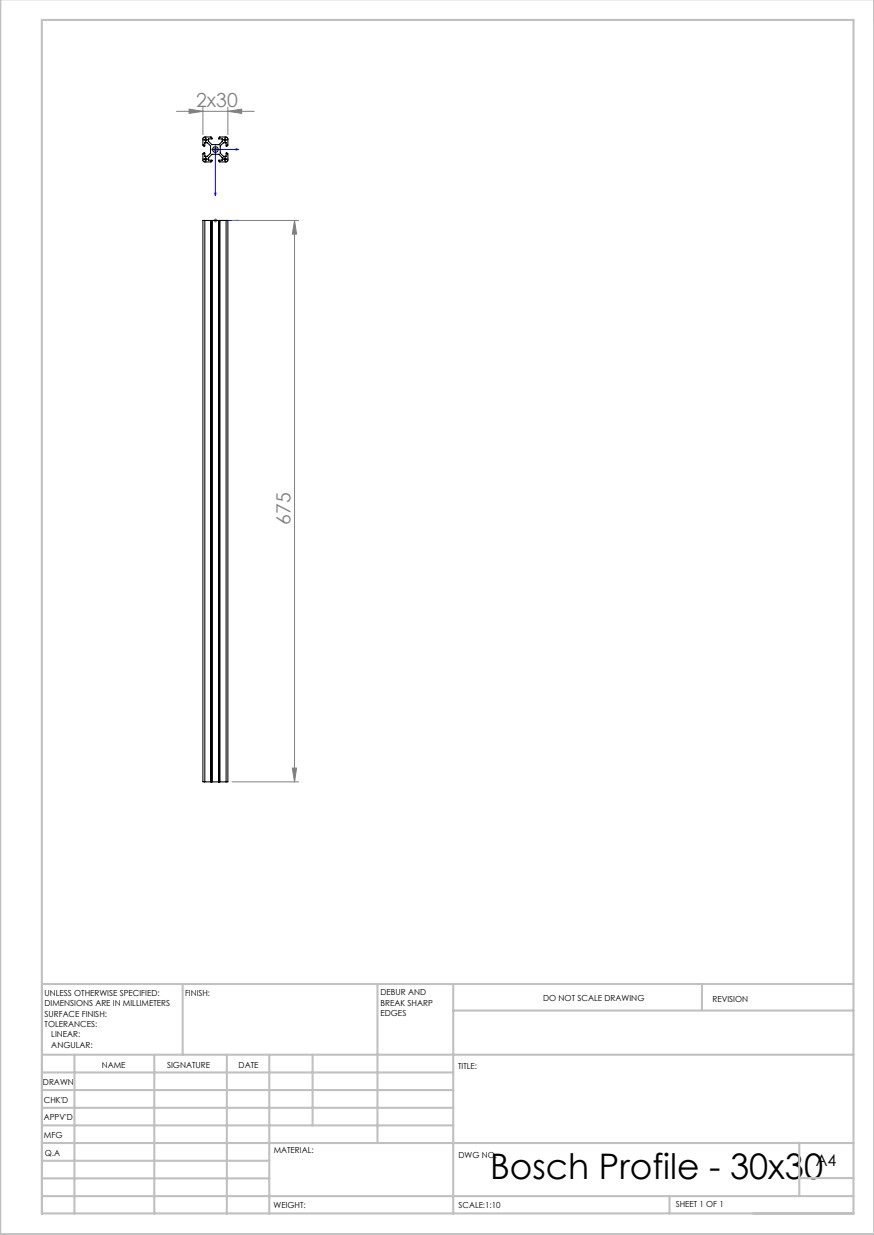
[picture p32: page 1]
SCALE:1:10; SHEET 1 OF 1; DO NOT SCALE DRAWING; REVISION; DEBUR AND BREAK SHARP; UNLESS OTHERWISE SPECIFIED:; FINISH:

DIMENSIONS ARE IN MILLIMETERS
SURFACE FINISH:
TOLERANCES:
LINEAR:
ANGULAR:

NAME | SIGNATURE | DATE | | | | TITLE:
Q.A | | | | MATERIAL: | Bosch Profile - 30x30 WEIGHT: DWG NO. | A4

DRAWN
CHK'D
APPV'D
MFG

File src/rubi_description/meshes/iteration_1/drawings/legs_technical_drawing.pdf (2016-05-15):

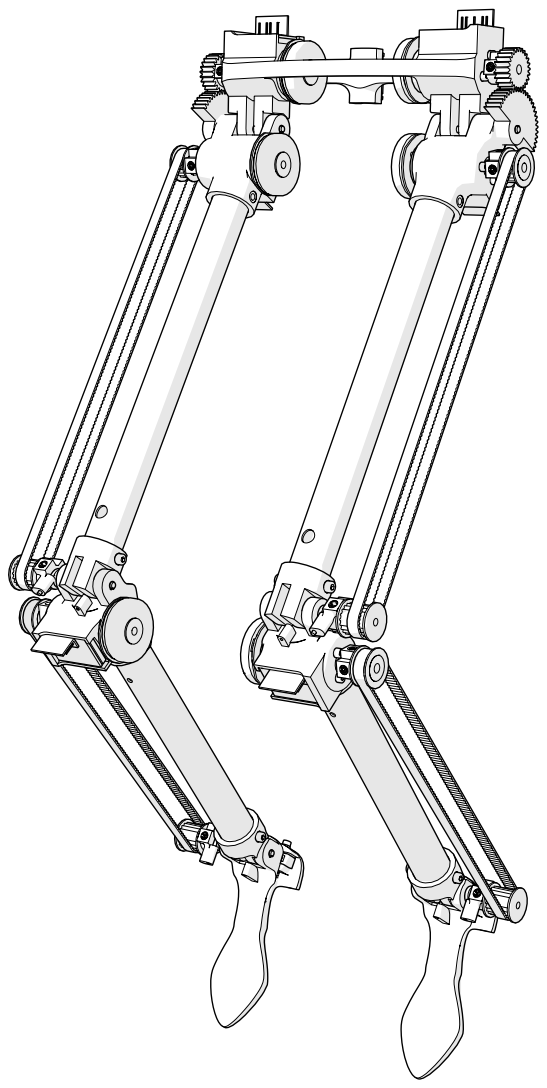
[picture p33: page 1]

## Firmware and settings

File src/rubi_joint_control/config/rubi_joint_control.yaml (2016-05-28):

# Publish all joint states
joint_states:
  type: joint_state_controller/JointStateController
  publish_rate: 50  

# Controllers 
# rubi_controllers:
#   type: effort_controllers/JointGroupEffortController
#   joints: 
#     - left_ankle
#     - left_knee
#     - left_hip
#     - right_ankle
#     - right_knee
#     - right_hip

# Effort Controllers
left_ankle_effort:
  type: effort_controllers/JointEffortController
  joint: left_ankle
left_knee_effort:
  type: effort_controllers/JointEffortController
  joint: left_knee
left_hip_effort:
  type: effort_controllers/JointEffortController
  joint: left_hip

right_ankle_effort:
  type: effort_controllers/JointEffortController
  joint: right_ankle
right_knee_effort:
  type: effort_controllers/JointEffortController
  joint: right_knee
right_hip_effort:
  type: effort_controllers/JointEffortController
  joint: right_hip

# Position Controllers
left_ankle_position:
  type: effort_controllers/JointPositionController
  joint: left_ankle
  pid: {p: 100.0, i: 0.01, d: 10.0}
left_knee_position:
  type: effort_controllers/JointPositionController
  joint: left_knee
  pid: {p: 100.0, i: 0.01, d: 10.0}
left_hip_position:
  type: effort_controllers/JointPositionController
  joint: left_hip
  pid: {p: 100.0, i: 0.01, d: 10.0}

right_ankle_position:
  type: effort_controllers/JointPositionController
  joint: right_ankle
  pid: {p: 100.0, i: 0.01, d: 10.0}
right_knee_position:
  type: effort_controllers/JointPositionController
  joint: right_knee
  pid: {p: 100.0, i: 0.01, d: 10.0}
right_hip_position:
  type: effort_controllers/JointPositionController
  joint: right_hip
  pid: {p: 100.0, i: 0.01, d: 10.0}

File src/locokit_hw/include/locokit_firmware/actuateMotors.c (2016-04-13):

///////////////////////////////////////
//				server Side
///////////////////////////////////////
//			Auther: Bassel Zeidan
///////////////////////////////////////
//This code opens the connection
//with the client side (a computer which controls the robot) and waits for the
//commands to operate.

#include <time.h>
#include <math.h>
#include <stdlib.h>
#include <stdio.h>
#include "locoapi.h"

#include <string.h>
#include <unistd.h>
#include <arpa/inet.h>
#include <sys/types.h>
#include <netinet/in.h>
#include <sys/socket.h>

#define PORT 1214 //connection port
#define false 0
#define true 1

struct sockaddr_in dest; /* socket info about the machine connecting to us */
struct sockaddr_in serv; /* socket info about our side */
int mysocket; /* socket used to listen for incoming connections */
socklen_t socksize;
int connected;
int termination_code;
int receiving_socket;
int sending_socket;
int print_commands;

int enable_command_printing;

/////////////////////////////////////////////////////////////////
/////////////////////Connection Functions////////////////////////
/////////////////////////////////////////////////////////////////
void define_server(short int port_number)
{
    enable_command_printing = false;
    memset(&serv, 0, sizeof(serv)); /* zero the struct before filling the fields */
    serv.sin_family = AF_INET; /* set the type of connection to TCP/IP */
    serv.sin_addr.s_addr = htonl(INADDR_ANY); /* set our address to any interface */
    serv.sin_port = htons(port_number); /* set the server port number */
    mysocket = socket(AF_INET, SOCK_STREAM, 0); //use tcp protocol
    /* bind serv information to mysocket */
    bind(mysocket, (struct sockaddr*)&serv, sizeof(struct sockaddr));
    connected = true;
    if (listen(mysocket, 1) == -1) {
        connected = false;
        printf("Error: listen(), can't listen on the socket...\n");
    }
}

int accept_a_client()
{ //returns client socket
    int connected_socket_descripter = accept(mysocket, (struct sockaddr*)&dest, &socksize);
    if (connected_socket_descripter == -1) {
        connected = false;
        printf("Error: accept(), can't connect to the socket and establish the connection...\n");
    }
    return connected_socket_descripter;
}

int send_command(int command, int client_socket)
{
    char* message;
    message = (char*)&command;
    int rec_res;
    rec_res = send(client_socket, message, sizeof(int), 0);
    if (rec_res == -1) {
        printf("Warning: send(), a message hasn't been sent...\n");
        return -1;
    }
    return 0;
}

/////////////////////////////////////////////////////////////////
///////////////////////////Control routines//////////////////////
/////////////////////////////////////////////////////////////////
//applying the pwm value on the targeted actuator
//takes the actuator ID as an input in addition to the pwm value
void PWM_control_routine(int act_number, float pwm)
{
    //Sets the controller mode
    setRegisterValueUI("CONTROLLER_MODE", act_number, 3);

    //Set the pmw value
    setActuatorPWM(pwm, act_number);
}

//applying the ConstantSpeedInterpolatingFunction
//values on the targeted actuator.
//it sets the motor control interpolation values.
//Parameters:
//actuator: The motor to control
//period: The period time in seconds
//phaseOffset: The phaseOffset in degrees
//directionNegative: the direction of rotation, 0 for rotation in positive direction 1 for negative
void ConstantSpeedInterpolatingFunction_control_routine(int act_number, float period,
    float phaseoffset, int direction)
{
    //Sets the controller mode of the legs
    setRegisterValueUI("CONTROLLER_MODE", act_number, 5);

    //Set the speed and sync of the legs (even numbers)
    setConstantSpeedInterpolatingFunction(act_number, period, phaseoffset, direction);
}

//stop a targeted actuator. Takes the actuator number as an input
void setActuatorStopped_routine(int act_number)
{
    setActuatorStopped(act_number);
}

//receives  setActuatorPWM parameters from the client and calls the required functions
//to execute the command.
//It takes the connected socket numebr as an input
//return 1 if successful, -1 errors, 0 connection is closed
int setActuatorPWM_command(int* socket)
{
    char buffer_int[sizeof(int)];
    char buffer_float[sizeof(float)];
    int rec_res;
    int act_number;
    float pwm;
    //get actuator number
    rec_res = recv(*socket, buffer_int, sizeof(int), 0);
    if (rec_res == -1) {
        printf("Warning: receive(), an error while receiving a message...\n");
        return -1;
    }
    else if (rec_res == 0) {
        printf("Warning: connection is closed...\n");
        return 0;
    }
    act_number = *((int*)buffer_int);
    //get pwm
    rec_res = recv(*socket, buffer_float, sizeof(float), 0);
    if (rec_res == -1) {
        printf("Warning: receive(), an error while receiving a message...\n");
        return -1;
    }
    else if (rec_res == 0) {
        printf("Warning: connection is closed...\n");
        return 0;
    }
    pwm = *((float*)buffer_float);
    if (enable_command_printing == true)
        printf("PWM command, Act = %i, PWM = %f\n", act_number, pwm);
    PWM_control_routine(act_number, pwm);
    return 1;
}

//receives  setConstantSpeedInterpolatingFunction parameters
//from the client and calls the required functions to
//execute the command (It calls (ConstantSpeedInterpolatingFunction_control_routine).
//It takes the connected socket numebr as an input
//return 1 if successful, -1 errors, 0 connection is closed
int setConstantSpeedInterpolatingFunction_command(int* socket)
{
    char buffer_int[sizeof(int)];
    char buffer_float[sizeof(float)];
    int rec_res;
    int act_number, direction;
    float period, phaseoffset;
    //get actuator number
    rec_res = recv(*socket, buffer_int, sizeof(int), 0);
    if (rec_res == -1) {
        printf("Warning: receive(), an error while receiving a message...\n");
        return -1;
    }
    else if (rec_res == 0) {
        printf("Warning: connection is closed...\n");
        return 0;
    }
    act_number = *((int*)buffer_int);
    //get period
    rec_res = recv(*socket, buffer_float, sizeof(float), 0);
    if (rec_res == -1) {
        printf("Warning: receive(), an error while receiving a message...\n");
        return -1;
    }
    else if (rec_res == 0) {
        printf("Warning: connection is closed...\n");
        return 0;
    }
    period = *((float*)buffer_float);
    //get phaseoffset
    rec_res = recv(*socket, buffer_float, sizeof(float), 0);
    if (rec_res == -1) {
        printf("Warning: receive(), an error while receiving a message...\n");
        return -1;
    }
    else if (rec_res == 0) {
        printf("Warning: connection is closed...\n");
        return 0;
    }
    phaseoffset = *((float*)buffer_float);
    //get direction
    rec_res = recv(*socket, buffer_int, sizeof(int), 0);
    if (rec_res == -1) {
        printf("Warning: receive(), an error while receiving a message...\n");
        return -1;
    }
    else if (rec_res == 0) {
        printf("Warning: connection is closed...\n");
        return 0;
    }
    direction = *((int*)buffer_int);
    if (enable_command_printing == true)
        printf("ConstantSpeedInterpolatingFunction command, act = %i, period = %f, phaseoffset = %f,  direction = %i\n", act_number, period, phaseoffset, direction);
    ConstantSpeedInterpolatingFunction_control_routine(act_number, period, phaseoffset, direction);
    return 1;
}

//receives  the targeted motor ID from the client and
//calls the required functions to execute the command
//(stop command for a specific motor).
//It takes the connected socket numebr as an input
//return 1 if successful, -1 errors, 0 connection is closed
int setActuatorStopped_command(int* socket)
{
    char buffer_int[sizeof(int)];
    int rec_res;
    int act_number;
    //get actuator number
    rec_res = recv(*socket, buffer_int, sizeof(int), 0);
    if (rec_res == -1) {
        printf("Warning: receive(), an error while receiving a message...\n");
        return -1;
    }
    else if (rec_res == 0) {
        printf("Warning: connection is closed...\n");
        return 0;
    }
    act_number = *((int*)buffer_int);
    //call pwm function//////////////////////////////////////////////////here
    if (enable_command_printing == true)
        printf("stop Actuator number %i\n", act_number);
    setActuatorStopped_routine(act_number);
    return 1;
}

//calls the required functions to get the number of sensors
//It takes the connected socket numebr as an input
//return 1 if successful, -1 errors, 0 connection is closed
int getNumberOfSensors_procedure(int* socket)
{
    int num_sensors = getNumberOfSensors();
    //printf("Number of sensors: \n", num_sensors);
    char* message;
    message = (char*)&num_sensors;
    int rec_res;
    rec_res = send(*socket, message, sizeof(int), 0);
    if (rec_res == -1) {
        printf("Warning: send(), a message hasn't been sent...\n");
        return -1;
    }
    return 1;
}

//receives  the targeted sensor ID from the client and
//calls the required functions to execute the function
//"getSensorValueRawFloat". It sends back the results to the client
//It takes the connected socket numebr as an input
//return 1 if successful, -1 errors, 0 connection is closed
int getSensorValueRawFloat_procedure(int* socket)
{
    //get sensor number
    char buffer_int[sizeof(int)];
    int rec_res;
    int sensor_number;
    rec_res = recv(*socket, buffer_int, sizeof(int), 0);
    if (rec_res == -1) {
        printf("Warning: receive(), an error while receiving a message...\n");
        return -1;
    }
    else if (rec_res == 0) {
        printf("Warning: connection is closed...\n");
        return 0;
    }
    sensor_number = *((int*)buffer_int);
    char* message;
    float value = getSensorValueRawFloat(sensor_number);
    message = (char*)&value;
    rec_res = send(*socket, message, sizeof(float), 0);
    if (rec_res == -1) {
        printf("Warning: send(), a message hasn't been sent...\n");
        return -1;
    }
    return 1;
}

//receives  the targeted sensor ID from the client and
//executes the function "getSensorValue" which get a sensor value.
//It sends back the results to the client
//It takes the connected socket numebr as an input
//return 1 if successful, -1 errors, 0 connection is closed
int getSensorValue_procedure(int* socket)
{
    //get sensor number
    char buffer_int[sizeof(int)];
    int rec_res;
    int sensor_number;
    rec_res = recv(*socket, buffer_int, sizeof(int), 0);
    if (rec_res == -1) {
        printf("Warning: receive(), an error while receiving a message...\n");
        return -1;
    }
    else if (rec_res == 0) {
        printf("Warning: connection is closed...\n");
        return 0;
    }
    sensor_number = *((int*)buffer_int);
    char* message;
    float value = getSensorValue(sensor_number);
    message = (char*)&value;
    rec_res = send(*socket, message, sizeof(float), 0);
    if (rec_res == -1) {
        printf("Warning: send(), a message hasn't been sent...\n");
        return -1;
    }
    return 1;
}

//receives  the targeted sensor ID from the client and
//executes the function "resetSensorValue" which reset a sensor.
//It sends back the results to the client
//It takes the connected socket numebr as an input
//return 1 if successful, -1 errors, 0 connection is closed
int resetSensorValue_procedure(int* socket)
{
    //get sensor number
    char buffer_int[sizeof(int)];
    int rec_res;
    int sensor_number;
    rec_res = recv(*socket, buffer_int, sizeof(int), 0);
    if (rec_res == -1) {
        printf("Warning: receive(), an error while receiving a message...\n");
        return -1;
    }
    else if (rec_res == 0) {
        printf("Warning: connection is closed...\n");
        return 0;
    }
    sensor_number = *((int*)buffer_int);
    resetSensorValue(sensor_number);
    return 1;
}

//executes the function "getSensorValueRawFloat" for all available sensors
//to get all sensors' values.
//It sends back the results to the client as an array of 6 elements
//sensor (0) ---> acc on x
//sensor (1) ---> acc on y
//sensor (2) ---> acc on z
//sensor (3) ---> gyo x
//sensor (4) ---> gyo y
//sensor (5) ---> gyo z
//It takes the connected socket numebr as an input
//return 1 if successful, -1 errors, 0 connection is closed
int getSensorValueRawFloat_array_procedure(int* socket)
{
    //get sensor number
    int rec_res;
    char* message;
    float send_buffer[6];
    int i;
    for (i = 0; i < 6; i++)
        send_buffer[i] = getSensorValueRawFloat(i);

    message = (char*)send_buffer;
    rec_res = send(*socket, message, sizeof(float) * 6, 0);
    if (rec_res == -1) {
        printf("Warning: send(), a message hasn't been sent...\n");
        return -1;
    }
    return 1;
}

//receives  the targeted motor ID from the client and
//executes the function "getActuatorVelocity" which gives the motor velocity.
//It sends back the results to the client
//It takes the connected socket numebr as an input
//return 1 if successful, -1 errors, 0 connection is closed
int getActuatorVelocity_procedure(int* socket)
{
    //get sensor number
    char buffer_int[sizeof(int)];
    int rec_res;
    int sensor_number;
    rec_res = recv(*socket, buffer_int, sizeof(int), 0);
    if (rec_res == -1) {
        printf("Warning: receive(), an error while receiving a message...\n");
        return -1;
    }
    else if (rec_res == 0) {
        printf("Warning: connection is closed...\n");
        return 0;
    }
    sensor_number = *((int*)buffer_int);
    char* message;
    float value = getActuatorVelocity(sensor_number);
    message = (char*)&value;
    rec_res = send(*socket, message, sizeof(float), 0);
    if (rec_res == -1) {
        printf("Warning: send(), a message hasn't been sent...\n");
        return -1;
    }
    return 1;
}

//receives  the targeted motor ID from the client and
//executes the function "getActuatorPosition" which gives the motor position.
//It sends back the results to the client
//It takes the connected socket numebr as an input
//return 1 if successful, -1 errors, 0 connection is closed
int getActuatorPosition_procedure(int* socket)
{
    //get sensor number
    char buffer_int[sizeof(int)];
    int rec_res;
    int sensor_number;
    rec_res = recv(*socket, buffer_int, sizeof(int), 0);
    if (rec_res == -1) {
        printf("Warning: receive(), an error while receiving a message...\n");
        return -1;
    }
    else if (rec_res == 0) {
        printf("Warning: connection is closed...\n");
        return 0;
    }
    sensor_number = *((int*)buffer_int);
    char* message;
    float value = getActuatorPosition(sensor_number);
    message = (char*)&value;
    rec_res = send(*socket, message, sizeof(float), 0);
    if (rec_res == -1) {
        printf("Warning: send(), a message hasn't been sent...\n");
        return -1;
    }
    return 1;
}

//receives  the targeted motor ID from the client and
//executes the function "getActuatorPWM" which gives the motor PMW.
//It sends back the results to the client
//It takes the connected socket numebr as an input
//return 1 if successful, -1 errors, 0 connection is closed
int getActuatorPWM_procedure(int* socket)
{
    //get sensor number
    char buffer_int[sizeof(int)];
    int rec_res;
    int sensor_number;
    rec_res = recv(*socket, buffer_int, sizeof(int), 0);
    if (rec_res == -1) {
        printf("Warning: receive(), an error while receiving a message...\n");
        return -1;
    }
    else if (rec_res == 0) {
        printf("Warning: connection is closed...\n");
        return 0;
    }
    sensor_number = *((int*)buffer_int);
    char* message;
    float value = getActuatorPWM(sensor_number);
    message = (char*)&value;
    rec_res = send(*socket, message, sizeof(float), 0);
    if (rec_res == -1) {
        printf("Warning: send(), a message hasn't been sent...\n");
        return -1;
    }
    return 1;
}

//this function represent the protocol interpreter which
//interprete the commands that are coming from client.
//It takes the command number as an input and the client socket
//2 ----> PWM control
//3 ----> ConstantSpeedInterpolatingFunction control
//4 ----> get Number Of Sensors
//5 ----> get Sensor Value RawFloat
//6 ----> get Sensor Value RawFloat_array (returns an array)
//7 ----> get Actuator Velocity
//8 ----> get Actuator Position
//9 ----> get Actuator PWM
//10 ----> stop an Actuator
//11 ----> get Sensor Value
//12 ----> reset Sensor Value
//50 ----> termination code
int command_interpreter(int command, int* socket)
{
    int res = -1;
    switch (command) {
    case 2: //PWM control
        res = setActuatorPWM_command(socket);
        break;
    case 3:
        res = setConstantSpeedInterpolatingFunction_command(socket);
        break;
    case 4:
        res = getNumberOfSensors_procedure(socket);
        break;
    case 5:
        res = getSensorValueRawFloat_procedure(socket);
        //sensor_value
        break;
    case 6:
        res = getSensorValueRawFloat_array_procedure(socket);
        //sensory_array
        break;
    case 7:
        res = getActuatorVelocity_procedure(socket);
        //velocity
        break;
    case 8:
        res = getActuatorPosition_procedure(socket);
        break;
    case 9:
        res = getActuatorPWM_procedure(socket);
        break;
    case 10:
        res = setActuatorStopped_command(socket);
        break;
    case 11:
        res = getSensorValue_procedure(socket);
        break;
    case 12:
        res = resetSensorValue_procedure(socket);
        break;
    case 50: //termination code
        termination_code = true;
        break;
    default: //res = -1;
        return -1; //quit code
        break;
    }
    return res;
}

/////////////////////////End Control Procedures//////////////////////
int receive_command(int* command, int* client_socket)
{
    char buffer[sizeof(int)];
    int rec_res;
    rec_res = recv(*client_socket, buffer, sizeof(int), 0);
    if (rec_res > 0) {
        *command = *((int*)buffer);
        return command_interpreter(*command, client_socket);
    }
    else if (rec_res == -1) {
        printf("Warning: receive(), an error while receiving a message...\n");
        return -1;
    }
    else if (rec_res == 0) {
        printf("Warning: connection is closed...\n");
        return 0;
    }
    return rec_res;
}

void receive_commands()
{
    int command;
    while (receive_command(&command, &receiving_socket) > 0) {
        //printf("received command = %i\n", command);
    }
}

int main(int argc, char* argv[])
{
    //initialize LocoAPI
    if (initializeLocoAPI("loco-settings.cfg") != 0) {
        printf("Failed to initialize LocoAPI\n");
        exit(-1);
    }

    termination_code = false;
    print_commands = false;

    socksize = sizeof(struct sockaddr_in);
    printf("Listening...\n");
    define_server(PORT);
    while (termination_code == 0) {
        printf("waiting for new socket...\n");
        receiving_socket = accept_a_client(); //wait for the first socket (receiving socket)
        printf("receiving connection is connected...\n");
        //sending_socket = accept_a_client();//wait for the first socket (receiving socket)
        //printf("sending connection is connected...\n");
        printf("a connection is established successfully with the w-lan controller...\n");
        if (!connected) {
            printf("a connection couldn't be established...\n");
            printf("Terminate program...\n");
            return -1;
        }
        //calling receive command procedure
        receive_commands();
        close(receiving_socket);
    }
    close(mysocket);
    freeLocoAPI();
    return 0;
}

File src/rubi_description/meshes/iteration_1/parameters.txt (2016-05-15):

"ankle_angle" = 70
"knee_angle"= 70
"hip_angle" = 30

"ankle_angle_max" = 120
"ankle_angle_min" = 50
"knee_angle_max" = 120
"knee_angle_min" = 0
"hip_angle_max" = 90
"hip_angle_min" = -60

"spring_ankle_parallel_arm_diameter"= 1.5
"spring_ankle_parallel_arm_length"= 13
"spring_ankle_parallel_intern_diameter"= 5.7
"spring_ankle_parallel_angle"= "ankle_angle"
"spring_ankle_parallel_turns"= 3
"spring_ankle_parallel_pitch"= "spring_ankle_parallel_arm_diameter" * 1.01
"spring_ankle_parallel_cutting_distance"= (1-"spring_ankle_parallel_angle" / 360) * "spring_ankle_parallel_pitch"
"spring_ankle_parallel_nominal_diameter"= "spring_ankle_parallel_arm_diameter" + "spring_ankle_parallel_intern_diameter"

"spring_ankle_serial_arm_diameter"= 1.91
"spring_ankle_serial_arm_length"= 10
"spring_ankle_serial_intern_diameter"= 5.7
"spring_ankle_serial_angle"= "90"
"spring_ankle_serial_turns"= 3
"spring_ankle_serial_pitch"= "spring_ankle_serial_arm_diameter" * 1.01
"spring_ankle_serial_cutting_distance"= (1-"spring_ankle_serial_angle" / 360) * "spring_ankle_serial_pitch"
"spring_ankle_serial_nominal_diameter"= "spring_ankle_serial_arm_diameter" + "spring_ankle_serial_intern_diameter"

"spring_knee_parallel_arm_diameter"= 1.5
"spring_knee_parallel_arm_length"= 13
"spring_knee_parallel_intern_diameter"= 5.7
"spring_knee_parallel_angle"= -"knee_angle" + 90
"spring_knee_parallel_turns"= 3
"spring_knee_parallel_pitch"= "spring_knee_parallel_arm_diameter" * 1.01
"spring_knee_parallel_cutting_distance"= (1-("spring_knee_parallel_angle") / 360) * "spring_knee_parallel_pitch"
"spring_knee_parallel_nominal_diameter"= "spring_knee_parallel_arm_diameter" + "spring_knee_parallel_intern_diameter"

"spring_knee_serial_arm_diameter"= 1.91
"spring_knee_serial_arm_length"= 10
"spring_knee_serial_intern_diameter"= 5.7
"spring_knee_serial_angle"= "90"
"spring_knee_serial_turns"= 3
"spring_knee_serial_pitch"= "spring_knee_serial_arm_diameter" * 1.01
"spring_knee_serial_cutting_distance"= (1-"spring_knee_serial_angle" / 360) * "spring_knee_serial_pitch"
"spring_knee_serial_nominal_diameter"= "spring_knee_serial_arm_diameter" + "spring_knee_serial_intern_diameter"

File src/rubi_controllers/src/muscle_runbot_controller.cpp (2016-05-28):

#include "muscle_runbot_controller.h"

MuscleRunbotController::MuscleRunbotController() : nh_("~") {
  steps = 0;
  pos = 0;
  nSensors = 6;
  nMotors = 6;

  gait = new runbot::cGaitTransition(runbot::cGaitProfile());
  nnet = new runbot::cNNet((runbot::cGaitProfile*)gait);

  /*
  newGait = new runbot::cGaitProfile(78, 97, 115, 175, 2, 1.5);
  nnetTwo = new runbot::cNNet((runbot::cGaitProfile*)newGait);

  gait3 = new runbot::cGaitProfile(78, 115, 115, 175, 2, 2.7);
  nnet3 = new runbot::cNNet((runbot::cGaitProfile*)gait3);

  DinLeft = new DynamicCpg(0.04);   // 0.04
  DinRight = new DynamicCpg(0.04);  // 0.04
  */
  actualAD = valarray<double>(6 + 1);
  // Parameters
  // Get parameter names
  nh_.param<std::string>("joint_states_topic", topic_joint_states_,
                         "/rubi/joint_states");
  nh_.param<std::string>("left_hip_topic", topic_left_hip_,
                         "/rubi/left_hip_effort/command");
  nh_.param<std::string>("left_knee_topic", topic_left_knee_,
                         "/rubi/left_knee_effort/command");
  nh_.param<std::string>("left_ankle_topic", topic_left_ankle_,
                         "/rubi/left_ankle_effort/command");
  nh_.param<std::string>("right_hip_topic", topic_right_hip_,
                         "/rubi/right_hip_effort/command");
  nh_.param<std::string>("right_knee_topic", topic_right_knee_,
                         "/rubi/right_knee_effort/command");
  nh_.param<std::string>("right_ankle_topic", topic_right_ankle_,
                         "/rubi/right_ankle_effort/command");
  nh_.param<std::string>("left_foot_contact_topic", topic_left_foot_contact_,
                         "/rubi/bumper/left_foot");
  nh_.param<std::string>("right_foot_contact_topic", topic_right_foot_contact_,
                         "/rubi/bumper/right_foot");

  // Subcribers
  sub_joint_states_ = nh_.subscribe<sensor_msgs::JointState>(
      topic_joint_states_, 1,
      &MuscleRunbotController::callbackSubcriberJointState, this);

  sub_left_foot_contact_ = nh_.subscribe<gazebo_msgs::ContactsState>(
      topic_left_foot_contact_, 1,
      &MuscleRunbotController::callbackSubcriberLeftFootContact, this);

  sub_right_foot_contact_ = nh_.subscribe<gazebo_msgs::ContactsState>(
      topic_right_foot_contact_, 1,
      &MuscleRunbotController::callbackSubcriberRightFootContact, this);

  // Publishers
  pub_left_ankle_ = nh_.advertise<std_msgs::Float64>(topic_left_ankle_, 1);
  pub_left_knee_ = nh_.advertise<std_msgs::Float64>(topic_left_knee_, 1);
  pub_left_hip_ = nh_.advertise<std_msgs::Float64>(topic_left_hip_, 1);
  pub_right_ankle_ = nh_.advertise<std_msgs::Float64>(topic_right_ankle_, 1);
  pub_right_knee_ = nh_.advertise<std_msgs::Float64>(topic_right_knee_, 1);
  pub_right_hip_ = nh_.advertise<std_msgs::Float64>(topic_right_hip_, 1);
  steps = 0;
  pos = 0;
  nSensors = 6;
  nMotors = 6;

  gait = new runbot::cGaitTransition(runbot::cGaitProfile());
  nnet = new runbot::cNNet((runbot::cGaitProfile*)gait);

  newGait = new runbot::cGaitProfile(78, 97, 115, 175, 2, 1.5);
  nnetTwo = new runbot::cNNet((runbot::cGaitProfile*)newGait);

  gait3 = new runbot::cGaitProfile(78, 115, 115, 175, 2, 2.7);
  nnet3 = new runbot::cNNet((runbot::cGaitProfile*)gait3);

  DinLeft = new DynamicCpg(0.04);   // 0.04
  DinRight = new DynamicCpg(0.04);  // 0.04

  actualAD = valarray<double>(6 + 1);
}

MuscleRunbotController::~MuscleRunbotController() {
  std_msgs::Float64 motor_msg;
  motor_msg.data = 0.0;

  pub_left_hip_.publish(motor_msg);
  pub_right_hip_.publish(motor_msg);
  pub_left_knee_.publish(motor_msg);
  pub_right_knee_.publish(motor_msg);

  delete DinLeft;
  delete DinRight;
  delete nnet;
  delete nnetTwo;
  delete gait;
  delete gait_two;
  delete newGait;
  delete gait3;
  delete nnet3;
}

void MuscleRunbotController::callbackSubcriberJointState(
    sensor_msgs::JointState msg) {
  std::unique_lock<std::mutex> lock(joint_state_mutex_);
  left_ankle_pos_ = msg.position.at(0);
  left_hip_pos_ = msg.position.at(1);
  left_knee_pos_ = msg.position.at(2);
  right_ankle_pos_ = msg.position.at(3);
  right_hip_pos_ = msg.position.at(4);
  right_knee_pos_ = msg.position.at(5);
}

void MuscleRunbotController::callbackSubcriberLeftFootContact(
    gazebo_msgs::ContactsState msg) {
  (msg.states.empty()) ? left_foot_contact_ = false : left_foot_contact_ = true;
}

void MuscleRunbotController::callbackSubcriberRightFootContact(
    gazebo_msgs::ContactsState msg) {
  (msg.states.empty()) ? right_foot_contact_ = false : right_foot_contact_ =
                                                           true;
}

void MuscleRunbotController::step() {
  valarray<double> motorOutput(4);
  steps++;

  actualAD[LEFT_HIP] = left_hip_pos_;
  actualAD[RIGHT_HIP] = right_hip_pos_;
  actualAD[LEFT_KNEE] = left_knee_pos_;
  actualAD[RIGHT_KNEE] = right_knee_pos_;
  actualAD[BOOM_ANGLE] = 0;
  actualAD[LEFT_FOOT] = left_ankle_pos_;
  actualAD[RIGHT_FOOT] = right_ankle_pos_;
  actualAD[0] = steps;

  // Used to generate 1 gait with reflexive nn
  motorOutput=nnet->update(actualAD,steps);

  // This is used to generate different gaits with the reflexive NN, change
  // according to your experiment
  /*
  if (steps < 5000)
    motorOutput = nnet->update(actualAD, steps);
  else if (steps >= 5000 && steps < 7000)
    motorOutput = nnetTwo->update(actualAD, steps);
  else
    motorOutput = nnet3->update(actualAD, steps);

  double enable;
  std::cout << steps << std::endl;

  double sensora;
  sensora = actualAD[LEFT_HIP];  // feedback
  std::vector<double> sign = DinLeft->generateOutputTwoLegThereshold(
      sensora, left_hip_effort_, left_knee_effort_,
      steps);  // generates motor signals
  DinLeft->setEnable(steps > 2000, left_hip_effort_, left_foot_contact_,
                     right_foot_contact_);  // generates enable output
  enable = DinLeft->getEnable();            // set enable
  std::cout << " enable: " << enable << std::endl;
  */

  // Depending on the enable, either reflexive signals or CPG-based are sent to
  // the motors
  std_msgs::Float64 motor_msg;


  left_hip_effort_ =
      motorOutput[0]/* * !enable + sign.at(0) * enable*/;  // LHMusclTor;
  motor_msg.data = -left_hip_effort_;
  pub_left_hip_.publish(motor_msg);

  right_hip_effort_ =
      motorOutput[1]/* * !enable + sign.at(1) * enable*/;  // RHMusclTor;
  motor_msg.data = -right_hip_effort_;
  pub_right_hip_.publish(motor_msg);

  left_knee_effort_ =
      motorOutput[2]/* * !enable + sign.at(2) * enable*/;  // LKMusclTor;
  motor_msg.data = -left_knee_effort_;
  pub_left_knee_.publish(motor_msg);

  right_knee_effort_ =
      motorOutput[3]/* * !enable + sign.at(3) * enable*/;  // RKMusclTor;
  motor_msg.data = -right_knee_effort_;
  pub_right_knee_.publish(motor_msg);

  // motors[4] = ubc + ubc_wabl;
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

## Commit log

2016-01-23 First commit with basic structure and files
    [model.sdf]
2016-01-23 Name changed to be more generic
    [model.sdf]
2016-01-23 Started description of the dacbot
    [model.sdf]
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2016-01-26 Updated to use macros
    [dacbot.urdf, dacbot.xacro]
2016-01-26 all parts added and compiles, but doesnt work yet!
    [dacbot.urdf, dacbot.xacro]
2016-01-26 it moves! the joint are wrong but it moves!
    [dacbot.xacro]
2016-01-31 Works in rviz but not in gazebo
    [dacbot.urdf, dacbot.xacro]
2016-01-31 risen a bit the robot in gazebo
    [dacbot.sdf]
2016-01-31 fixed scale problems. The problem with gazebo its due to the moemnts of inertia are really small
    [dacbot.urdf, dacbot.xacro]
2016-01-31 Set a minimum intertia value to avoid problems in gazebo
    [dacbot.urdf, dacbot.xacro]
2016-01-31 Using another property and reduced minimum intertia to 0.002
    [dacbot.urdf, dacbot.xacro]
2016-02-10 Body fixed
    [dacbot.urdf, dacbot.xacro]
2016-02-14 Added virtual transmission for mapping the output from the controller to the actuator
    [dacbot.urdf, dacbot.xacro]
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2016-02-14 changed name. Turned in to a ros package so we can search resources from xacro. Added rotational robot holder
    [model.sdf, rotational_robot_holder.xacro]
2016-02-14 added rotational robot holder
    [dacbot.urdf, dacbot.xacro]
2016-02-14 Changed from rotational to fixed the joint between the rotational robot holder and the robot
    [rotational_robot_holder.xacro]
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2016-02-17 Added feet contact sensors making use of the bumper plugin
    [dacbot.urdf, dacbot.xacro]
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2016-02-17 Added an extra dof to allow movemnt in z axis
    [rotational_robot_holder.xacro]
2016-02-19 Attach the holder to the side of the robot, not the middle
    [rotational_robot_holder.xacro]
2016-02-19 Added limits to the joints
    [dacbot.xacro]
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2016-02-26 The description of the rotational platform is now inside of the robot description so we can use the flag "robot floating" to debug the gaits
    [dacbot.xacro]
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2016-02-26 joints limits and damping parameters as xacro properties
    [dacbot.xacro]
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2016-03-09 added docs and first meshes
    [Legs.SLDASM, foot_left.SLDPRT, foot_left.STL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]
2016-03-14 added calculation of the flexion
    [profile_selection.xlsx]
2016-03-14 Added structure and move files to iteration folder
    [DIN 912 M3 x 10 --- 10N.sldprt, DIN 912 M3 x 20 --- 20N.sldprt, Hexagon Nut ISO 4032 - M3 - D - N.sldprt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]
2016-03-17 First prototype of the legs achieved. We need now to define motors and spring and adapt the model
    [DIN 912 M3 x 10 --- 10N.sldprt, GP22C_2-STUFIG-143976.sldprt, Legs.SLDASM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]
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2016-03-24 Separate dacbot_individual and dacbot_boxes where in the first one each link has its own propperties
    [dacbot_boxes.xacro]
2016-03-24 come back to the original file
    [dacbot_boxes.xacro]
2016-03-24 created legs from dacbot
    [colors.xacro, legs.xacro, model.sdf]
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2016-03-24 updated values to iteration 1
    [legs.xacro]
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2016-03-25 added node and service to restart simulation and start with the init positions
    [legs.xacro]
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2016-03-25 added relative angles for the links
    [Legs.SLDASM, foot_left.SLDPRT, foot_spring_holder_left.SLDPRT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]
2016-03-27 added initial positions as dynamic parameters
    [impulse.cfg, two_neuron.cfg]
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2016-03-27 implemented impulse with one leg and with two. Problems when restarting.
    [impulse_controller.cpp]
2016-03-27 Easier to change the controllers from the joints. Added hopping positions to the dynamic parameters
    [impulse.cfg]
2016-03-27 corrected initial hopping angles
    [impulse.cfg]
2016-03-27 corrected initial pos
    [Legs.SLDASM]
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2016-03-27 fixed bug in the update rate thread and adjusted link limits
    [impulse.cfg]
2016-03-27 fixed bug in the update rate thread
    [two_neuron_controller.cpp]
2016-03-27 fixed bugs when creating the limits of the feeet
    [legs.xacro]
2016-03-27 Fixed bug with the joint limits and added delay with real time factor when publishing the trajectory
    [impulse.cfg]
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2016-03-28 switched from rotational holder to virtual joints
    [legs.xacro]
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2016-04-02 added parametric springs and paramter control file
    [Legs.SLDASM, Motor.SLDASM, parameters.txt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]
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2016-04-03 redesigned ankle
    [Legs.SLDASM, ankle_left.SLDPRT, foot_left.SLDPRT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]
2016-04-03 foot redesigned. Now the springs are fitted in a hole
    [Legs.SLDASM, ankle_left.SLDPRT, foot_left.SLDPRT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]
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2016-04-04 pre-redesign knee. Motor model fixed and verified. Added fastener ISO 4029
    [GP22C_2-STUFIG-143976.sldprt, Legs.SLDASM, Maxon - Combination 432941.SLDASM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]
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2016-04-08 started with the redesign of the hip
    [Legs.SLDASM, Pulley - GT2 20 tooth.SLDPRT, ankle_left.SLDPRT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]
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2016-04-09 fixed coordinate systems
    [foot_left.SLDPRT]
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2016-04-11 Fixed some assembly bugs
    [Legs.SLDASM, Maxon - Combination 432941.SLDASM, MirrorStructure - right side.SLDPRT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]
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2016-04-13 moved files to its folders in tree structure
    [Legs.SLDASM]
2016-04-16 Updated model to the proportions of the mathematical mode
    [Legs.SLDASM, Mirrorknee_motor_holder_left.SLDPRT, belt_gt2_hip.SLDPRT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]
2016-04-16 changed name to simplify search path when creating the urdf
    [Bearing - LBBR8 341-1504.SLDPRT, DIN 912 M2.5 x 8 --- 8N.sldprt, DIN 912 M3 x 10 --- 10N.sldprt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]
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2016-04-16 added links from solidoworks. The model loads in gazebo and rviz
    [legs.xacro]
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2016-04-19 Commit with real inertias. Stack gazebo doesnt work with such small intertias. Thus, either we compile gazebo with other physic simulator or we increase the inertias. Both will be tried.
    [legs.urdf, legs.xacro]
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2016-04-19 copies from legs.xacro and added false intertias of 0.002
    [legs_false_inertias.xacro]
2016-04-19 added script to install gazebo with other physic models. Not finished
    [impulse.cfg, loco-settings.cfg, two_neuron.cfg]
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2016-04-20 Added holders for the electronics and the contact senros
    [Contact sensor.SLDPRT, DIN 912 M2.5 x 10 --- 10N.sldprt, DIN 912 M2.5 x 16 --- 16N.sldprt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]
2016-04-20 fixed bug with the color of the motor's electronics
    [MirrorMaxon - Extensor.SLDPRT]
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2016-04-24 structure of main added. Missing real time control
    [locokit_hw_interface.cpp, robot_configuration.h]
2016-04-24 added scale for visual, mass and inertias components
    [legs.xacro]
2016-04-24 fixed some cleareances
    [Mirrorankle_left.SLDPRT, Mirrorhip_motor_holder_left.SLDPRT, Mirrorknee_motor_holder_left.SLDPRT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]
2016-04-24 fixed bug when scaling the rotational holder
    [dacbot.xacro]
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2016-04-25 fixed some issues with read()
    [locokit_hw_interface.cpp]
2016-04-26 fixed bug in legs_false_inertias_world.launch
    [locokit_hw_interface.cpp, robot_configuration.h]
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2016-05-02 Fixed small walls
    [hip.SLDPRT, hip.STL]
2016-05-02 changed part's name to make them more congruent and fixed some cleareances
    [Legs and Environment.SLDASM, MirrorT2,5 6mm 19teeth.SLDPRT, Mirrorankle_left.SLDPRT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]
2016-05-02 fixed some bugs, added stls and BOM
    [Interface - Robot holder.SLDPRT, Interface - Robot holder.STL, Printed Parts - Profile - Robot.SLDPRT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]
2016-05-02 added holes to the structure for the cables
    [Mirrorhip_structure.SLDPRT, Mirrorknee_structure.SLDPRT, hip_structure.SLDPRT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]
2016-05-02 adjusted rods and added drawings for mechanical manufatured parts
    [ankle_rod.SLDPRT, hip_rod.SLDDRW, hip_structure.SLDDRW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]
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2016-05-05 Added method to give an impulse from a yaml file
    [Legs and Environment.SLDASM, MirrorT2,5 6mm 19teeth.SLDPRT, Mirrorhip_pinion.SLDPRT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]
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2016-05-11 reinforced pinion
    [Mirrorhip_pinion.SLDPRT, hip_pinion.SLDPRT, hip_pinion.STL]
2016-05-11 fixed some warnings from clang code
    [impulse_controller.cpp]
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2016-05-12 fixed some bugs and added flag for using the rotational holder or just have the robot floating
    [legs.xacro]
2016-05-12 fixed joint limits of the ankle
    [legs.xacro]
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2016-05-13 fixed scaling factors
    [legs.xacro]
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2016-05-21 fixsed som mistaques and aded som guords to de cri di printin part
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2016-05-22 serial pulley illustrations needs fix
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2016-05-24 corrected cha 5 introduction + pulleybelt sec
2016-05-24 gears section corrected
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2016-05-27 format change to book. corrected page numbering and changed to book due to the thesis must be given printed
2016-05-28 changed name of EVERYTHING from legs to rubi. Everything needs to be re-checked
    [Bearing - LBBR8 341-1504.SLDPRT, Contact sensor.SLDPRT, DIN 912 M2.5 x 10 --- 10N.sldprt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]
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2016-05-29 missing joints image in Ankle and knee joints mechanics Sec
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2016-05-29 correcting Springs integration
2016-05-29 sec ankle and knee joints corrected
2016-05-29 CAD design section corrected
2016-05-30 Experimental framework Ch corrected, V2
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2016-06-03 broken down the repo into src, media and docs. Thus, not the whole repo needs to downloaded
    [Costs.ods, Hip gears parameters.xlsx, belt_tension_calculator.xls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]
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
